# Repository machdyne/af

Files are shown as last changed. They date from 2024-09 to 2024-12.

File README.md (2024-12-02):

# Machdyne AF

## Overview

Machdyne AF is an open-source project for a PNP autofeeder system[^1].

The autofeeder design is a closed-loop system that uses an infrared LED and phototransistor array[^2] to precisely detect the tape position. The tape is moved forward using a geared DC motor and a sprocket. The cover tape is partially separated and advanced with the tape.

The autofeeders can be chained together with 4 wires and communicate with the system controller using the I2C protocol.

The system uses two custom printed circuit board designs. An autofeeder controller PCB (Essen) includes the tape detection and motor driver circuitry for each autofeeder. A system controller PCB (Koch) provides power and allows a chain of feeders to communicate with the OpenPnP software over a USB-C port.

[^1]: This project is still under development and is not yet suitable for use in production.
[^2]: While the PCB has an array of six phototransistors, the firmware is currently using only one.

## Autofeeder 3D parts (AF1)

| Model | Image | Description |
| ----- | ----- | --- |
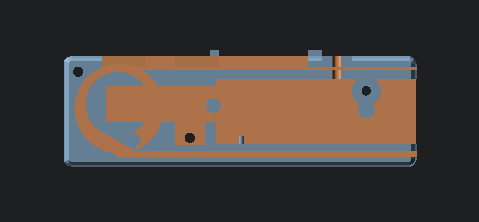
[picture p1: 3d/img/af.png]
| [af](3d/stl/af.stl) |  | The autofeeder body guides the tape and holds the Essen PCB in place |
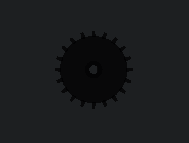
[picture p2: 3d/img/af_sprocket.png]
| [af_sprocket](3d/stl/af_sprocket.stl) |  | The sprocket advances the tape |
| [af_motor_lock](3d/stl/af_motor_lock.stl) | af_motor_lock | The motor lock holds the motor in place |
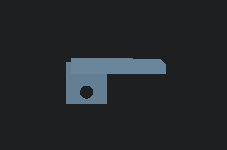
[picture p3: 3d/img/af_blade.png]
af_blade
| [af_blade](3d/stl/af_blade.stl) |  | The blade partially peels the clear film from the top of the tape to the side |
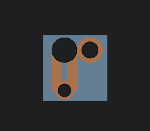
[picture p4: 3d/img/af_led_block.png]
af_led_block
| [af_led_block](3d/stl/af_led_block.stl) |  | The LED block holds the LED in place |
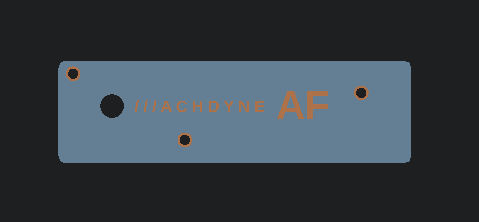
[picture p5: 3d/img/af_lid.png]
af_lid
| [af_lid](3d/stl/af_lid.stl) |  | The lid closes the autofeeder and guides the tape |

### Bill of Materials

| Part | Quantity | Description | Example P/N |
| ---- | --- | --- | --- |
| Worm gear motor | 1 | Right-angle N20 DC 12V 16 RPM | JGY-N20 |
| LED | 1 | 3mm 940nm 1.3Vf Infrared LED | DY-FIR204C |
| M3 bolt 12mm + nut | 1 | for blade | - |
| M3 screw 20mm countersunk | 1 | for LED block | - |
| M3 bolt 20mm countersunk + nut | 3 | for lid | - |
| M3 bolt 25mm | 1 | to connect LED block to rail |
| M3 T3 nut | 1 | to connect LED block to rail |

You will also need dupont jumper wires to connect the motor and LED to Essen.

### Assembly Instructions

Cut, strip and solder one end of the jumper wires to the motor leads and each lead of the LED. Press the LED into the LED block, and run the wires through the large LED block hole.

Attach the blade using an M3 bolt and nut.

Press the sprocket onto the motor axle. Press the motor into the motor cavity.

Run the LED wires through the rear autofeeder hole and connect to Essen LED\_A and LED\_K. Connect the motor wires to Essen MOT1 and MOT2.

Push the PCB onto the PCB notches so that it locks into place.

Attach the LED block using the screw.

Place the motor lock on top of the motor.

Attach the lid.

Connect Essen to Koch or other Essens using a 4-pin female-female 2.54mm dupont cable.

Attach the LED block to a 2020 rail with an M3 bolt and T-nut.

The assembled autofeeder (without lid):

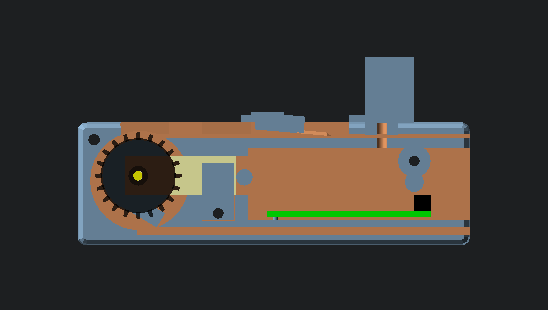
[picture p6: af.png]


## Autofeeder controller PCB (Essen)

Also see the [firmware and usage instructions](fw/essen).

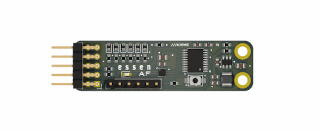
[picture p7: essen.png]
Essen


### Pinout (Rear)

```
9  7  5  3  1
10 8  6  4  2
```

| Pin | Signal | Notes |
| --- | --- | ----- |
| 9/10 | 12V | System power input |
| 7/8 | GND | Ground |
| 5/6 | SDA | I2C data |
| 3/4 | SCL | I2C clock |
| 2 | TRIGGER | Optional external tape advance signal |
| 1 | SWDIO | MCU SWD signal for firmware updates / serial debugging output |

### Pinout (Top)

| Pin | Signal | Notes |
| --- | --- | ----- |
| 1 | MOT1 | Motor driver output #1 |
| 2 | GND | Ground |
| 3 | MOT2 | Motor driver output #2 |
| 4 | GND | Ground |
| 5 | ELED\_A | External (IR) LED anode |
| 6 | ELED\_K | External (IR) LED cathode |

The motor driver can drive one bidirectional motor or two unidirectional motors.

## System controller PCB (Koch)

Also see the [firmware and usage instructions](fw/koch).

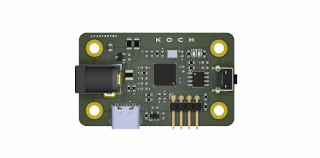
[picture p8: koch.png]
Koch


### Pinout

```
1 2 3 4
```

| Pin | Signal | Notes |
| --- | --- | ----- |
| 1 | 12V | System power output (2.5mm positive tip) |
| 2 | GND | System ground |
| 3 | SDA | I2C data |
| 4 | SCL | I2C clock |

## Funding

This project is being partially funded through the [NGI0 Entrust Fund](https://nlnet.nl/entrust/), a fund established by NLnet with financial support from the European Commission's Next Generation Internet programme.

## License

This project is released under the [CERN-OHL-P](LICENSE.txt) license.

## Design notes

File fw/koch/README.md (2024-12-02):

# Koch Firmware

Koch is the autofeeder system controller PCB for the [Machdyne AF](https://github.com/machdyne/af) project.

This firmwire provides a minimal G-code compatible interface over the USB port that can be driven by an OpenPnP GcodeDriver.

Each feeder has an 1-byte ID, which is set when the Essen firmware is built.

## Building

To build the RP2040 firmware, assuming you have [pico-sdk](https://github.com/raspberrypi/pico-sdk) installed:

```
$ mkdir build
$ cd build
$ cmake ..
$ make
```

## OpenPnp Configuration

### Machine Setup

Add a GCodeDriver under Drivers and set the correct serial port, 115200 baud.

Set the driver Gcode value for ACTUATE\_DOUBLE\_COMMAND:

```
K100 {IntegerValue}
```

Add an Actuator that uses the above driver with Value Type of Double.

### Feeder Setup

Add a new feeder and select the above actuator, set the actuator value to the decimal I2C ID of the feeder.

## Gcode Commands

| Command | Description |
| --- | --- |
| K100 \<feeder\_id\> | Advance the specified feeder (ID is base-10) |
| K200 | Motor on full forward |
| K201 | Motor on full reverse |
| K202 | Motor off |
| K900 | Report system status & current usage |

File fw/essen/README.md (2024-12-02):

# Essen Firmware

Essen is the autofeeder controller PCB for the [Machdyne AF](https://github.com/machdyne/af) project.

This firmware controls the autofeeder and accepts I2C commands from the system controller (Koch).

Each feeder has an 1-byte ID, which is set when the firmware is built.

The sensor may need to be calibrated by changing the AF\_THRES definitions.

## Building

To build the firmware you need to have a RISC-V toolchian installed, see [ch32v003fun](https://github.com/cnlohr/ch32v003fun/wiki/Installation) for setup instructions.

To build the firmware and program Essen (via the SWDIO pin):

```
$ make
```

## License

Essen uses ch32V003fun which is released under the MIT license.

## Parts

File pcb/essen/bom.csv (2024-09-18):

Id | Designator | Footprint | Quantity | Designation | Supplier and ref
1 | R13,R9,R3,R10,R11,R12,R4 | R_0603_1608Metric | 7 | 10K
2 | H1,H2 | MountingHole_2.7mm_M2.5_ISO14580_Pad | 2 | MountingHole_Pad
3 | L1 | L_1210_3225Metric | 1 | 3.3uH 1.2A
4 | U3 | WSON-8-1EP_2x2mm_P0.5mm_EP0.9x1.6mm_ThermalVias | 1 | DRV8220
5 | C9,C10 | C_0603_1608Metric | 2 | 22uF
6 | Q7,Q6,Q4,Q8,Q5,Q3 | D_0603_1608Metric | 6 | Q_Photo_NPN | XL-1608PDC
7 | C8,C6 | C_0603_1608Metric | 2 | 100nF16v
8 | U1 | TSSOP-20_4.4x6.5mm_P0.65mm | 1 | CH32V003F4P6
9 | C3 | C_0805_2012Metric | 1 | 22uF25v
10 | J2 | PinHeader_1x06_P2.54mm_Vertical | 1 | Conn_01x06_Pin
11 | C1 | C_0603_1608Metric | 1 | 100nF
12 | SW3 | Button_2P_3x4mm | 1 | SW_Push
13 | R1 | R_0603_1608Metric | 1 | 1K
14 | F1 | Fuse_0603_1608Metric | 1 | 500mA Hold 1A Trip 15V
15 | C7 | C_0805_2012Metric | 1 | 10uF16v
16 | R6,R7 | R_0603_1608Metric | 2 | 100R
17 | D1 | LED_0603_1608Metric | 1 | LED
18 | U4 | TSOT-23-6 | 1 | AP62300TWU-7
19 | C2 | C_0603_1608Metric | 1 | 10uF
20 | R2 | R_0603_1608Metric | 1 | 33K2
21 | J1 | PinHeader_2x05_P2.54mm_Horizontal | 1 | Conn_02x05_Odd_Even
22 | G*** | ld-kicad | 1 | LOGO

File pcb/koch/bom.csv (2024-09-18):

Id | Designator | Footprint | Quantity | Designation | Supplier and ref
1 | C6,C5,C8,C14,C12,C4,C13,C7 | C_0603_1608Metric | 8 | 100nF
2 | C2,C1 | C_0603_1608Metric | 2 | 15pF
3 | R12,R2,R6 | R_0603_1608Metric | 3 | 5K1
4 | R7 | R_0603_1608Metric | 1 | 10K
5 | C3,C18,C15,C10 | C_0603_1608Metric | 4 | 1uF
6 | J3 | BarrelJack_GCT_DCJ200-10-A_Horizontal | 1 | Barrel_Jack
7 | D2 | LED_0603_1608Metric | 1 | LEDR
8 | R13 | R_1206_3216Metric | 1 | 4K7
9 | R4,R3 | R_0603_1608Metric | 2 | 27R
10 | H1,H4,H2,H3 | MountingHole_3.2mm_M3_ISO14580_Pad | 4 | MountingHole_Pad
11 | R1,R14 | R_0603_1608Metric | 2 | 536R
12 | U2 | SOIC-8_3.9x4.9mm_P1.27mm | 1 | W25Q32JVSS
13 | J2 | PinHeader_1x04_P2.54mm_Horizontal | 1 | Conn_01x04_Pin
14 | F1 | Fuse_1210_3225Metric | 1 | 2.6A HOLD 5A TRIP 24V
15 | U4 | SOT-23 | 1 | ZXCT1107
16 | U3 | TSOP-5_1.65x3.05mm_P0.95mm | 1 | NCP115
17 | D1 | LED_0603_1608Metric | 1 | LEDG
18 | C11 | C_0603_1608Metric | 1 | 10pF50v
19 | C17 | C_0603_1608Metric | 1 | 4.7uF
20 | U1 | RP2040-QFN-56-OFFICIAL | 1 | RP2040
21 | J1 | USB_C_Receptacle_HRO_TYPE-C-31-M-12-BIG-PADS | 1 | TYPE-C-31-M-12-FIXED
22 | R8,R5 | R_0603_1608Metric | 2 | 1K
23 | SW3 | SW_Tactile_SPST_Angled_PTS645Vx39-2LFS | 1 | BOOT
24 | C16 | C_0805_2012Metric | 1 | 22uF16v
25 | R9,R10 | R_0603_1608Metric | 2 | 4K7
26 | R11 | R_1206_3216Metric | 1 | 50mOhm
27 | FB1 | R_0603_1608Metric | 1 | Ferrite_Bead
28 | Y1 | XTAL_ECS-240-8-33-AGN-TR | 1 | ECS-80-12-33-JGN-TR-12MHZ

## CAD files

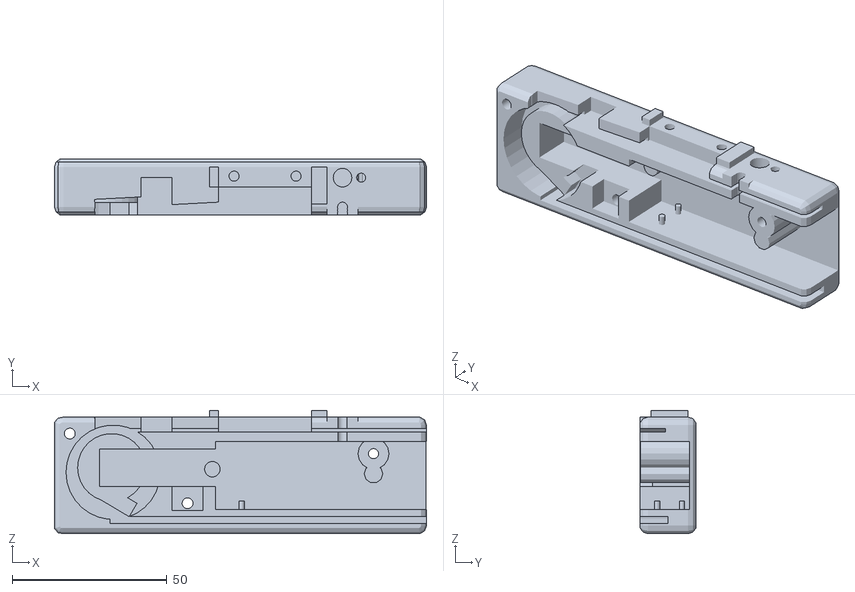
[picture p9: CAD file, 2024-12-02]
3d/stl/af.stl
120.0 x 18.0 x 39.8

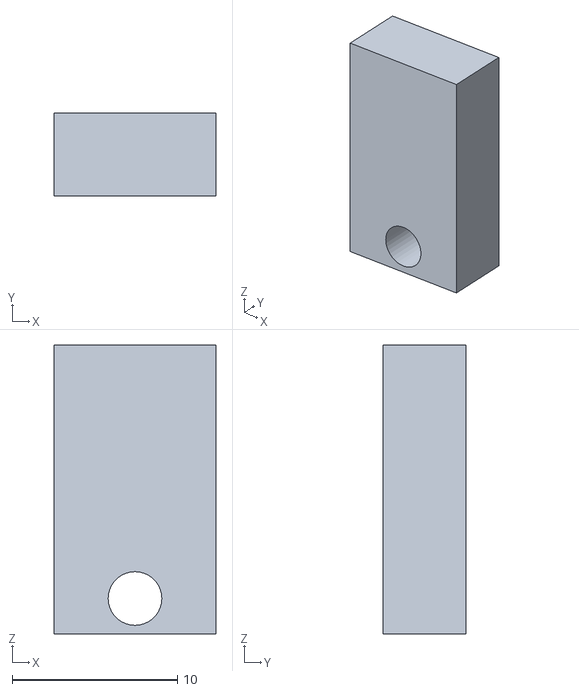
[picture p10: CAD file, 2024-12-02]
3d/stl/af_motor_lock.stl
9.80 x 5.00 x 17.5

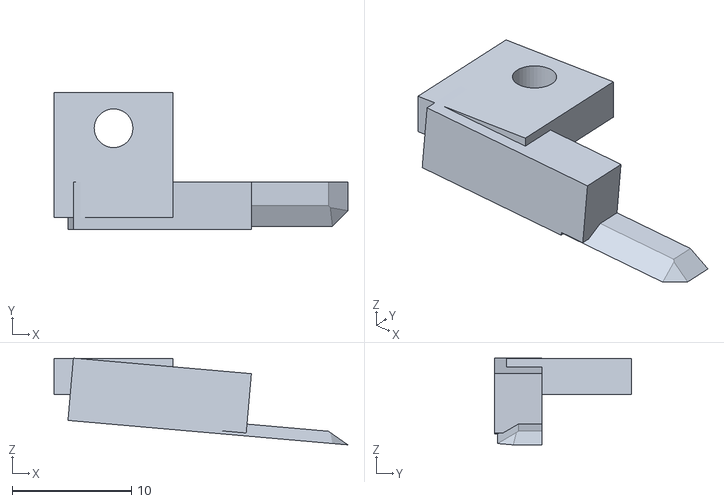
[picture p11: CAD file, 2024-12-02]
3d/stl/af_blade.stl
24.7 x 11.5 x 7.29

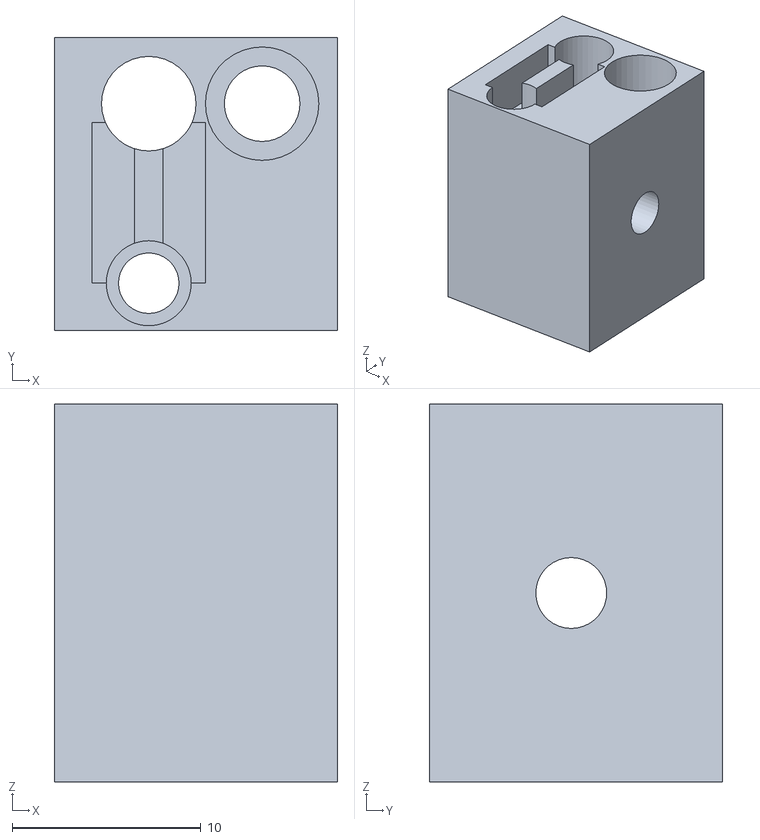
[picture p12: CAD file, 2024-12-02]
3d/stl/af_led_block.stl
15.0 x 15.5 x 20.0

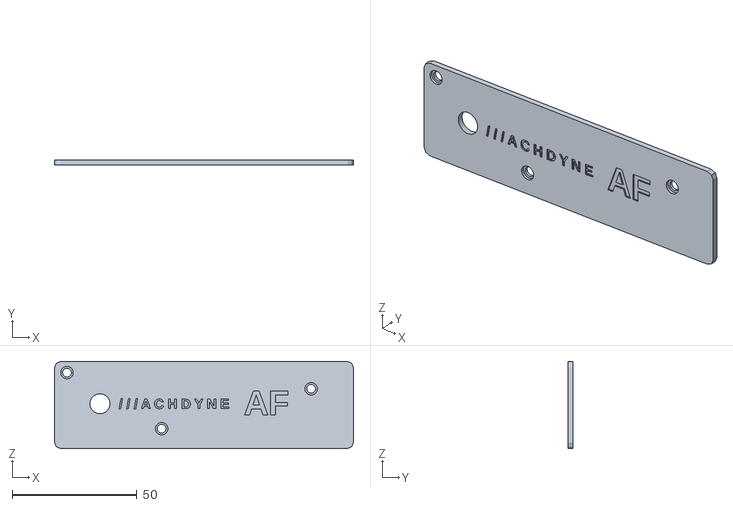
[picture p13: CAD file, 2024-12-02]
3d/stl/af_lid.stl
120.0 x 2.00 x 35.0

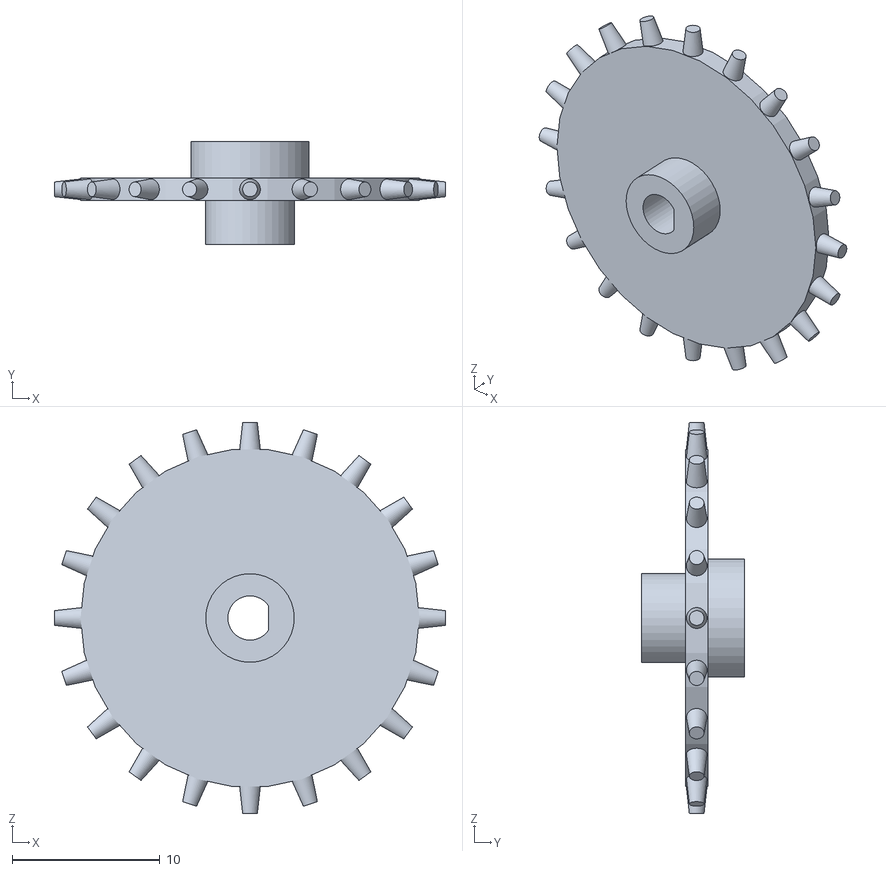
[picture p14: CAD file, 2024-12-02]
3d/stl/af_sprocket.stl
26.5 x 7.00 x 26.5

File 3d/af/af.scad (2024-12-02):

/*
 * PnP Autofeeder
 * Copyright (c) 2024 Lone Dynamics Corporation. All rights reserved.
 * 
 */

tape_width = 8.2;
tape_thickness = 1.2;
tape_pitch = 4;

gear_spokes = 20;
gear_d = gear_spokes * tape_pitch / PI;

rotate([90,0,0]) {
	
	af();

	translate([0,11.75,0]) af_led_block();
	
	af_motor_lock();
	translate([0,0.85,0]) af_blade();
//	translate([0,0.85,0]) af_film_puller();
//	translate([0,0,10]) af_lid();
	
//	translate([-100,12,0.9]) af_tape();

	color([0,0,0,0.5]) rotate([270,0,0]) translate([-44.5,-5,0.5]) af_sprocket();
	
	rotate([270,180,0]) translate([-85,-7,-12]) af_pcb();
	rotate([90,0,180]) translate([22.75,-2,0.5]) af_tape_motor();

}

module af_tape() {
	color([1,1,1]) cube([200,1,8]);
	
}

module af_tape_motor(margin=0) {
	 
	 translate([8.75,0,-0]) color([1,1,0.7]) cube([34, 10+margin, 12+margin], center=true);


	 color([1,1,0]) translate([16.5+9-3.5,8.5,0]) rotate([90,0,0])
		cylinder(d=3, h=7.5, center=true, $fn=36);

}

module af_pcb() {
	color([0,1,0]) translate([40,0,0]) cube([50,15,1.6]);
	color([0,0,0]) translate([40,0,1.6]) cube([5,15,5]);
}

module af_sprocket() {
	gear_spokes = 20;
	difference() {
		union() {
			for (i = [0:gear_spokes-1]) {
				rotate([90,0,90]) translate([-2.75,0,0])
					rotate([i*(360/gear_spokes),0,0])
						translate([0,0,11])
							cylinder(d1=1.5, d2=1, h=2.25, $fn=36);
			}
			rotate([90,0,0]) translate([0,0,2]) cylinder(d=gear_d-2.5, h=1.5);
			rotate([90,0,0]) translate([0,0,-0.5]) cylinder(d=8, h=3.5, $fn=36);
			rotate([90,0,0]) translate([0,0,3]) cylinder(d=6, h=3.5, $fn=36);
			
		}
		rotate([90,0,0]) difference() {
			translate([0,0,2]) cylinder(d=3, h=20, center=true, $fn=36);
			translate([1.75,0,2]) cube([1,10,10], center=true);
		}
		
	}
}

module af_lid() {
	
	difference() {

		union() {
			translate([-126/2,-35/2-1.5,-2/2]) roundedcube(120,35,2,2.5);
		}
		
		// bolt holes
		translate([40,5,-20]) cylinder(d=3.5, h=50, $fn=36);
		translate([-20,-11,-20]) cylinder(d=3.5, h=50, $fn=36);
		translate([-58,11.5,-20]) cylinder(d=3.5, h=50, $fn=36);
		
		// flush mount bolt holes
		translate([40,5,0]) cylinder(d=5, h=50, $fn=36);
		translate([-20,-11,0]) cylinder(d=5, h=50, $fn=36);
		translate([-58,11.5,0]) cylinder(d=5, h=50, $fn=36);

		// axle
		translate([-44.75,0.5,-5]) cylinder(d=8, h=50, $fn=36);

		// logo
		translate([-15,-1.5,0.5])
				linear_extrude(5)
					text("/ / / A C H D Y N E", size=4, halign="center",
						font="Liberation Sans:style=Bold");		

		translate([20,-4,0.5])
				linear_extrude(5)
					text("AF", size=10, halign="center",
						font="Liberation Sans:style=Bold");		
		
	}
}

module af_blade() {
	
	union() {
	
		// blade mount
		difference() {
			translate([-10,16,-6.5]) cube([10,3,10.5]);
			translate([-5,20,-3.5]) rotate([90,0,0])
				cylinder(d=3.25, h=10, $fn=36);
		}
		
		rotate([0,0,-5]) {
			
			translate([-10,13.25,1]) cube([15,5,4]);

			// film blade
			translate([0,0,0]) rotate([0,0,0]) difference() {

				translate([-10,13,1]) cube([25,1,4]);
				translate([11,14.5,0.5]) rotate([0,0,-30]) cube([25,2,4]);
				translate([3,14,3]) rotate([30,0,0]) cube([25,2,4]);
				translate([5,14,10]) rotate([35,45,0]) cube([25,2,4]);

			}

		}
	
	}
}

module af_film_puller() {

			
	union() {
	
		// blade mount
		difference() {
			translate([-10,16,-6.5]) cube([30,19,12]);
			
			// bolt holes
			translate([-5,50,-3.5]) rotate([90,0,0])
				cylinder(d=3.25, h=100, $fn=36);
			translate([15,50,-3.5]) rotate([90,0,0])
				cylinder(d=3.25, h=100, $fn=36);
			
			translate([-5,36,-3.5]) rotate([90,0,0])
				cylinder(d=5, h=2, $fn=36);
			translate([15,36,-3.5]) rotate([90,0,0])
				cylinder(d=5, h=2, $fn=36);
			
			// motor cutout
			translate([5-(12.25/2),28,-5.75]) cube([12.25,50,10.25]);
			translate([5-(10.5/2),29,-5.75]) cube([10.5,50,15.5]);
			
			// gear axle
			translate([5,22,-10]) rotate([0,0,0])
				cylinder(d=3.5, h=50, $fn=36);
				//cylinder(d=3.25, h=50, $fn=36);


	
		}
		
	}


}
		
module af_motor_lock() {
	difference() {
		translate([-25+0.1,-7.25-5.9,3.4]) cube([9.8,17.5,5]);
		translate([-20,-11,-20]) cylinder(d=3.25, h=50, $fn=36);
	}
}

module af_led_block() {
	
	difference() {
		
		// LED block
		translate([25,25,-6.5]) rotate([90,0,0]) cube([15,15.5,20]);

		// LED mount
		translate([30,28,6.5]) rotate([90,0,0]) cylinder(d=4.5, h=15, $fn=36);
		translate([30,28,6.5]) rotate([90,0,0]) cylinder(d=3.2, h=25, $fn=36);
		
		// lead separator
		translate([27,26,-2]) rotate([90,0,0]) cube([2.25,8.5,5]);
		translate([30.75,26,-2]) rotate([90,0,0]) cube([2.25,8.5,5]);
		
		// LED block screw hole
		translate([36,20,-3]) rotate([90,0,0]) cylinder(d=4, h=35, center=true, 
			$fn=36);

		translate([36,24,-3]) rotate([90,0,0]) cylinder(d=6, h=5, center=true, 
			$fn=36);

		// rail mount hole
		translate([36,15,1.5]) rotate([0,90,0]) cylinder(d=3.75, h=35, center=true, $fn=36);

		// wire escape
		translate([30,10,-3]) rotate([90,0,0]) cylinder(d=6, h=35, center=true, 
			$fn=36);
	}

}

module af() {

// rail:
//	color([0,0,0]) translate([50,27,0]) cube([20,20,100], center=true);
	
	difference() {
		translate([40,5,-7.19]) cylinder(d=10, h=16);
		translate([40,5,-20]) cylinder(d=3.25, h=50, $fn=36);
		translate([40,5,-11]) cylinder(d=7, h=5, $fn=6);
	}
	
	translate([40,-9+7.5,-7.19]) cylinder(d=6, h=16);
		
	// blade lock
	translate([-13,19,-6.5]) rotate([90,0,0])
		cube([3,6.5,3]);

	// led block lock
	translate([20,19,-6.5]) rotate([90,0,0])
		cube([5,12,3]);

	// rear motor lock
	translate([-12,0,-8]) cylinder(d=5, h=5, $fn=36);

	difference() {
		translate([-44.5,0.5,0]) cylinder(d=gear_d-3.5, h=5);
		translate([-23.5,0.5,3.25]) {
			cube([50, 12.1, 20.5], center=true);
		}
		

	}
		
	// tape exit guide
	translate([-45.5,-5.55,-0]) rotate([90,0,-30.75]) cube([10.7,5,5]);
	
	// pcb mount notches
	translate([55-57.5,-10.25,-4.5]) rotate([90,0,0])
		cylinder(d=1.75, h=5, $fn=36);
	translate([55-57.5,-13.25,-4.5]) rotate([90,0,0])
		cylinder(d=3, h=1, $fn=36);
	translate([55-57.5,-10.25,-4.5+8]) rotate([90,0,0])
		cylinder(d=1.75, h=5, $fn=36);
	translate([55-57.5,-13.25,-4.5+8]) rotate([90,0,0])
		cylinder(d=3, h=1, $fn=36);

	difference() {
			
		union() {
			
			minkowski() {
				translate([-3,-2,0]) cube([120-5,37.5-5,18-5], center=true);
				sphere(2.6);
			}
			
			// LED block platform
			translate([25,16.81,-6.5]) rotate([90,0,0]) cube([10,15.5,3.75]);
				
		}
		
		// pick position
		translate([-35,12,-3]) cube([10,50,10]);
		
		// film guide
		translate([-50,12,7]) rotate([0,3,0]) cube([50,50,10]);
		translate([-10,12,0]) cube([30,50,20]);
		translate([1,13.1,0]) rotate([0,-30,25]) cube([5,5,5]);

		// film guide post pick
		translate([-50,12,4]) rotate([0,3,0]) cube([20,50,10]);
		
		// blade mount / film motor mount
		translate([-5,20,-3.5]) rotate([90,0,0])
			cylinder(d=3.25, h=15, $fn=36);

		translate([15,20,-3.5]) rotate([90,0,0])
			cylinder(d=3.25, h=15, $fn=36);
		
		// LED light channel
		translate([30,28,6.5]) rotate([90,0,0]) cylinder(d=3.2, h=20, $fn=36);
		translate([30,28,7.5]) rotate([90,0,0]) cylinder(d=3.2, h=20, $fn=36);
		translate([30,28,8.5]) rotate([90,0,0]) cylinder(d=3.2, h=20, $fn=36);
		
		// LED / motor wire escape
		translate([30,10,-3]) rotate([90,0,0]) cylinder(d=6, h=35, center=true, 
			$fn=36);

		// LED block screw hole
		translate([36,20,-3]) rotate([90,0,0]) cylinder(d=2.9, h=25, center=true, 
			$fn=36);

		// bolt holes
		translate([40,5,-20]) cylinder(d=3.5, h=50, $fn=36);
		translate([-20,-11,-20]) cylinder(d=3.5, h=50, $fn=36);
		translate([-58,11.5,-20]) cylinder(d=3.5, h=50, $fn=36);
		
		// nut holes
		translate([40,5,-11]) cylinder(d=7, h=5, $fn=6);
		translate([-20,-11,-11]) cylinder(d=7, h=5, $fn=6);
		translate([-58,11.5,-11]) rotate([0,0,30]) cylinder(d=7, h=5, $fn=6);
					
		// tape entrance cutout
		translate([-45,12,0.8]) cube([200,tape_thickness,tape_width]);
		translate([-45,12,0]) cube([12,tape_thickness,tape_width]);

		// tape exit cutout
		translate([-45,-17.5,0.0]) cube([200,tape_thickness+1,tape_width+1]);

		// motor cutout
		translate([-23.5,0.5,3.25]) {
			cube([50, 12.1, 20.5], center=true);
		}
		
		// motor lock cutout
		translate([-25,-7.25-6,3.4]) cube([10,10,5.6]);

		// sprocket cutout
		translate([-44,-1,0]) cylinder(d=gear_d+5, h=50);
		
		// pcb cutout
		translate([24,-2,1]) cube([70,22,16], center=true);
		
	}
	
}

// https://gist.github.com/tinkerology/ae257c5340a33ee2f149ff3ae97d9826
module roundedcube(xx, yy, height, radius)
{
    translate([0,0,height/2])
    hull()
    {
        translate([radius,radius,0])
        cylinder(height,radius,radius,true);

        translate([xx-radius,radius,0])
        cylinder(height,radius,radius,true);

        translate([xx-radius,yy-radius,0])
        cylinder(height,radius,radius,true);

        translate([radius,yy-radius,0])
        cylinder(height,radius,radius,true);
    }
}

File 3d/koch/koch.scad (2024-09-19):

/*
 * Koch Case
 * Copyright (c) 2024 Lone Dynamics Corporation. All rights reserved.
 *
 * required hardware (stand alone):
 *  - 4 x M3 x 20mm countersunk bolts
 *  - 4 x M3 nuts
 * 
 * required hardware (rail mount):
 *  - 2 x M3 x 20mm countersunk bolts
 *  - 2 x M3 x 25mm countersunk bolts
 *  - 2 x M3 nuts
 *  - 2 x M3 T-nuts
 *
 */

$fn = 100;

board_width = 30;
board_thickness = 1.5;
board_length = 50;
board_height = 1.6;
board_spacing = 2;

wall = 1.5;

top_height = 14;
bottom_height = 6;

translate([wall,wall,0]) afc_board();

translate([0,0,15])
	afc_case_top();

translate([0,0,-15])
	afc_case_bottom();

module afc_board() {
	
	difference() {
		color([0,0.5,0])
			roundedcube(board_width,board_length,board_thickness,5);
		translate([5, 5, -1]) cylinder(d=3.2, h=10);
		translate([5, 45, -1]) cylinder(d=3.2, h=10);
		translate([25, 5, -1]) cylinder(d=3.2, h=10);
		translate([25, 45, -1]) cylinder(d=3.2, h=10);
	}	
	
}

module afc_case_top() {
	

	difference() {
				
		color([0.5,0.5,0.5])
			roundedcube(board_width+(wall*2),board_length+(wall*2),top_height,5);

		// cutouts
			
		translate([1.5,9.5,-2])
			roundedcube(board_width,board_length-16,14.5,5);

		translate([9.5,2,-2])
			roundedcube(board_width-16,board_length,10.25,5);			
	
		translate([wall, wall, 0]) {

			// vents
			translate([25-(15/2),25,0]) rotate([0,0,-10]) cube([10,1,20]);
			translate([25-(15/2),20,0]) rotate([0,0,-10]) cube([10,1,20]);
			translate([25-(15/2),30,0]) rotate([0,0,-10]) cube([10,1,20]);			

			// POWER JACK
			translate([15-(9.5/2),30,-2]) cube([9.5,30,11.25+1.75]);

			// BOOT BUTTON
			translate([15-(7.6/2),-2,-2]) cube([7.6,30,7+1.75]);

			// USBC
			translate([-2,50-15-(10.5/2),-2]) cube([30,10.5,3.5+1.75]);

			// PNP CHAIN CONNECTOR
			translate([-2,50-34.2-(11/2),-2]) cube([30,11,3+1.75]);


			// bolt holes
			translate([5, 5, -21]) cylinder(d=3.5, h=40);
			translate([5, 45, -21]) cylinder(d=3.5, h=40);
			translate([25, 5, -20]) cylinder(d=3.5, h=40);
			translate([25, 45, -21]) cylinder(d=3.5, h=40);

			// flush mount bolt holes
			translate([5, 5, top_height-1.5]) cylinder(d=5.25, h=4);
			translate([5, 45, top_height-1.5]) cylinder(d=5.25, h=4);
			translate([25, 5, top_height-1.5]) cylinder(d=5.25, h=4);
			translate([25, 45, top_height-1.5]) cylinder(d=5.25, h=4);

			// koch text
			rotate(270)
				translate([-25,3.5,top_height-0.5])
					linear_extrude(1)
						text("K O C H", size=4, halign="center",
							font="Ubuntu:style=Bold");

		}
		
	}	
}

module afc_case_bottom() {
	
	difference() {
		color([0.5,0.5,0.5])
			roundedcube(board_width+(wall*2),board_length+(wall*2),bottom_height,5);
		
		// cutouts
		translate([3,10,1.5])
			roundedcube(board_width-3,board_length-17,10,5);
				
		translate([10.5,2.5,1.5])
			roundedcube(board_width-17.5,board_length-2,10,5);

		translate([wall, wall, 0]) {
			
		// board cutout
		translate([0,0,bottom_height-board_height])
			roundedcube(board_width+0.2,board_length+0.2,board_height+1,2.5);

		translate([wall, wall, 0]) {

			// USBC
			translate([30.5,43,5]) cube([10.20,15,10.5+1]);

		}

		// bolt holes
		translate([5, 5, -11]) cylinder(d=3.2, h=25);
		translate([5, 45, -11]) cylinder(d=3.2, h=25);
		translate([25, 5, -11]) cylinder(d=3.2, h=25);
		translate([25, 45, -11]) cylinder(d=3.2, h=25);

		// nut holes
		translate([5, 5, -1]) cylinder(d=7, h=4, $fn=6);
		translate([5, 45, -1]) cylinder(d=7, h=4, $fn=6);
		translate([25, 5, -1]) cylinder(d=7, h=4, $fn=6);
		translate([25, 45, -1]) cylinder(d=7, h=4, $fn=6);

		}
		
	}	
}

// https://gist.github.com/tinkerology/ae257c5340a33ee2f149ff3ae97d9826
module roundedcube(xx, yy, height, radius)
{
    translate([0,0,height/2])
    hull()
    {
        translate([radius,radius,0])
        cylinder(height,radius,radius,true);

        translate([xx-radius,radius,0])
        cylinder(height,radius,radius,true);

        translate([xx-radius,yy-radius,0])
        cylinder(height,radius,radius,true);

        translate([radius,yy-radius,0])
        cylinder(height,radius,radius,true);
    }
}

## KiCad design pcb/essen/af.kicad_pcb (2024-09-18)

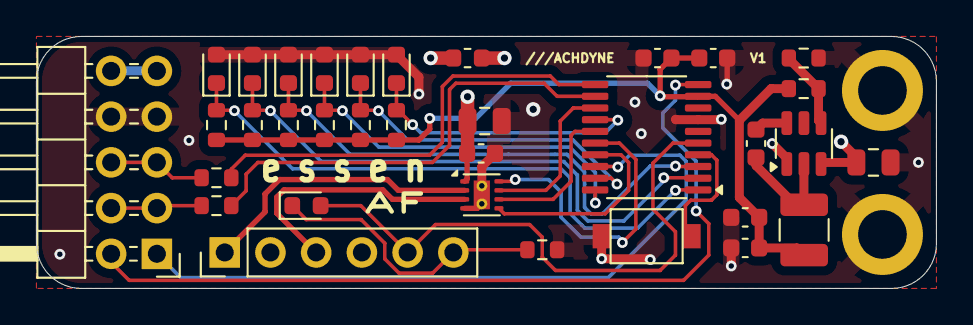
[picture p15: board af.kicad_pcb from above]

Board: 2 copper layers, 50.0 x 14.0 mm, 36 parts (0 on the bottom side), 28 nets.

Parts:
C1: 100nF; C_0603_1608Metric
C2: 10uF; C_0603_1608Metric
C3: 22uF25v; C_0805_2012Metric
C6, C8: 100nF16v; C_0603_1608Metric
C7: 10uF16v; C_0805_2012Metric
C9, C10: 22uF; C_0603_1608Metric
D1: LED; LED_0603_1608Metric
F1: 500mA Hold 1A Trip 15V; Fuse_0603_1608Metric
H1, H2: MountingHole_Pad; MountingHole_2.7mm_M2.5_ISO14580_Pad
J1: Conn_02x05_Odd_Even; PinHeader_2x05_P2.54mm_Horizontal
J2: Conn_01x06_Pin; PinHeader_1x06_P2.54mm_Vertical
L1: 3.3uH 1.2A; L_1210_3225Metric
Q3, Q4, Q5, Q6, Q7, Q8: Q_Photo_NPN; D_0603_1608Metric
R1: 1K; R_0603_1608Metric
R2: 33K2; R_0603_1608Metric
R3, R4, R9, R10, R11, R12, R13: 10K; R_0603_1608Metric
R6, R7: 100R; R_0603_1608Metric
SW3: SW_Push; Button_2P_3x4mm
U1: CH32V003F4P6; TSSOP-20_4.4x6.5mm_P0.65mm
U3: DRV8220; WSON-8-1EP_2x2mm_P0.5mm_EP0.9x1.6mm_ThermalVias
U4: AP62300TWU-7; TSOT-23-6

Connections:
/A2: Q8.1 (C), R13.2, U1.14 (PC4)
/A3: Q7.1 (C), R12.2, U1.19 (PD2)
/A4: Q6.1 (C), R11.2, U1.20 (PD3)
/A5: Q4.1 (C), R9.2, U1.2 (PD5)
/A6: Q5.1 (C), R10.2, U1.3 (PD6)
/A7: Q3.1 (C), R4.2, U1.1 (PD4)
/DRV_IN1: U1.15 (PC5), U3.6 (IN1)
/DRV_IN2: U1.17 (PC7), U3.5 (IN2)
/DRV_MODE: U1.13 (PC3), U3.7 (MODE)
/DRV_SLP: U1.16 (PC6), U3.8 (SLEEP_N)
/ELED_A: D1.2 (A), J2.5, U1.5 (PA1)
/ELED_K: D1.1 (K), J2.6, R1.2
/MOT1: J2.1, U3.2 (OUT1)
/MOT2: J2.3, U3.3 (OUT2)
/PWR3V3: C1.1, C2.1, C9.1, C10.1, L1.2, R2.2, R4.1, R9.1, R10.1, R11.1, R12.1, R13.1, U1.9 (VDD)
/PWRIN: C3.1, C6.1, C7.1, F1.2, U3.1 (VM), U4.3 (VIN)
/PWRINC: F1.1, J1.9, J1.10
/RESET: SW3.1, U1.4 (PD7)
/SCL: R7.2, U1.12 (PC2)
/SCLC: J1.3, J1.4, R7.1
/SDA: R6.2, U1.11 (PC1)
/SDAC: J1.5, J1.6, R6.1
/SW: C8.2, L1.1, U4.2 (SW)
/SWDIO: J1.1, U1.18 (PD1)
/TRIGGER: J1.2, U1.10 (PC0)
GND: C1.2, C2.2, C3.2, C6.2, C7.2, C9.2, C10.2, H1.1, H2.1, J1.7, J1.8, J2.2, J2.4, Q3.2 (E), Q4.2 (E), Q5.2 (E), Q6.2 (E), Q7.2 (E), Q8.2 (E), R1.1, R3.1, SW3.2, U1.7 (VSS), U3.4 (GND), U3.9 (EP), U4.1 (GND)
unnamed: C8.1, U4.6 (BST)
unnamed: R2.1, R3.2, U4.4 (FB)

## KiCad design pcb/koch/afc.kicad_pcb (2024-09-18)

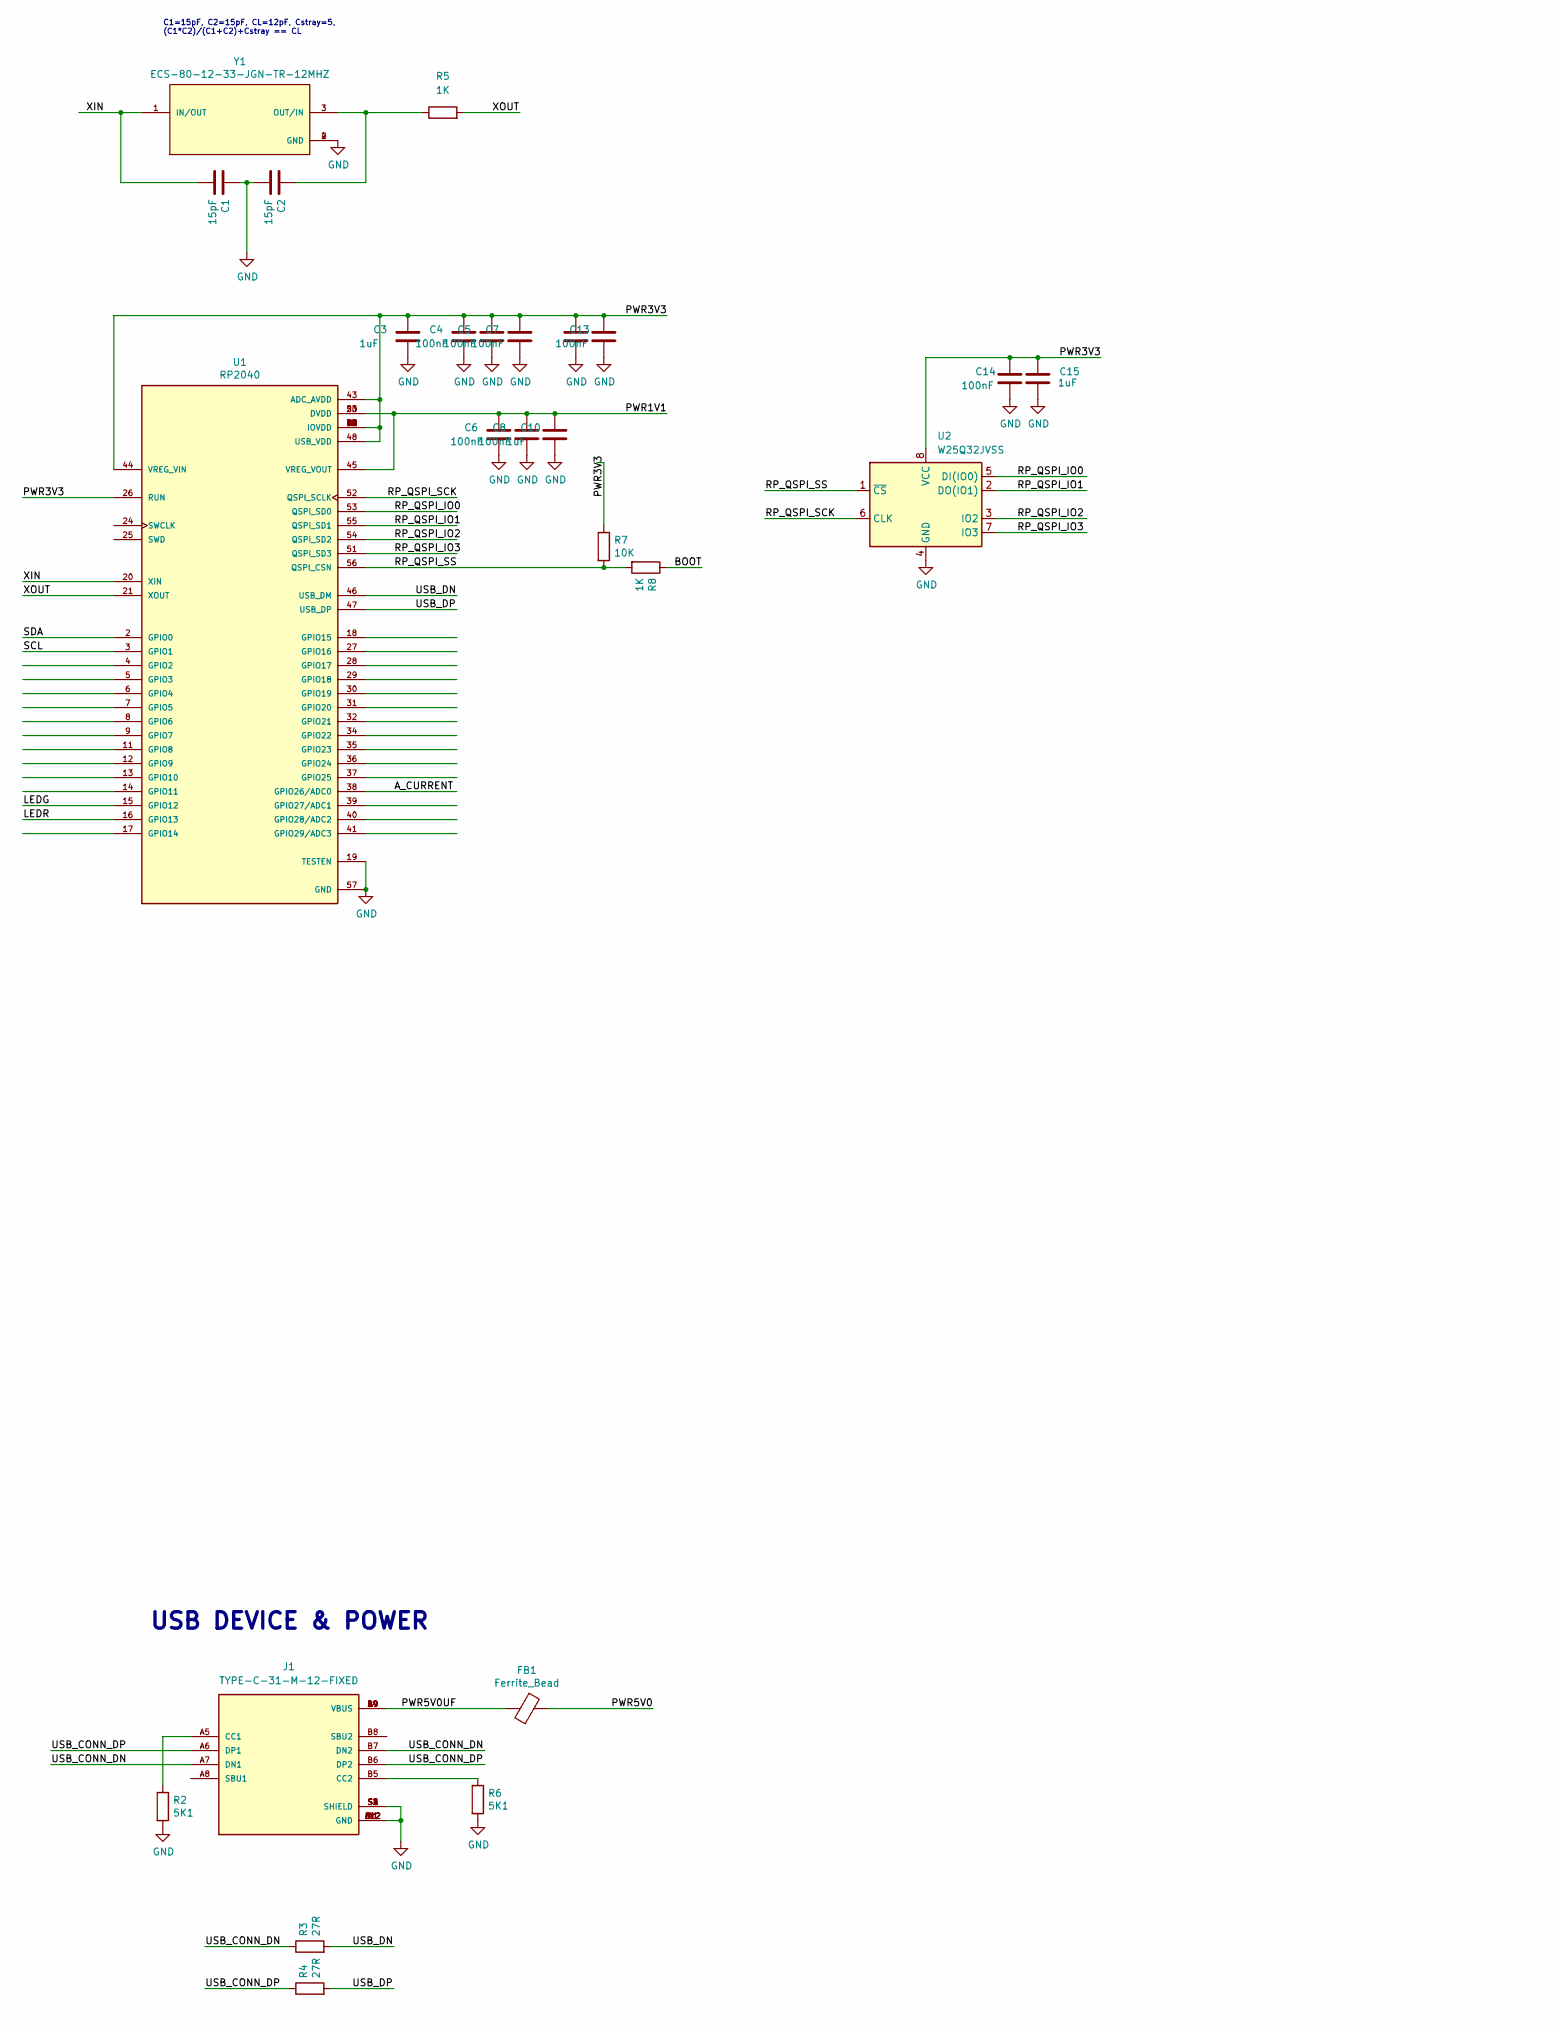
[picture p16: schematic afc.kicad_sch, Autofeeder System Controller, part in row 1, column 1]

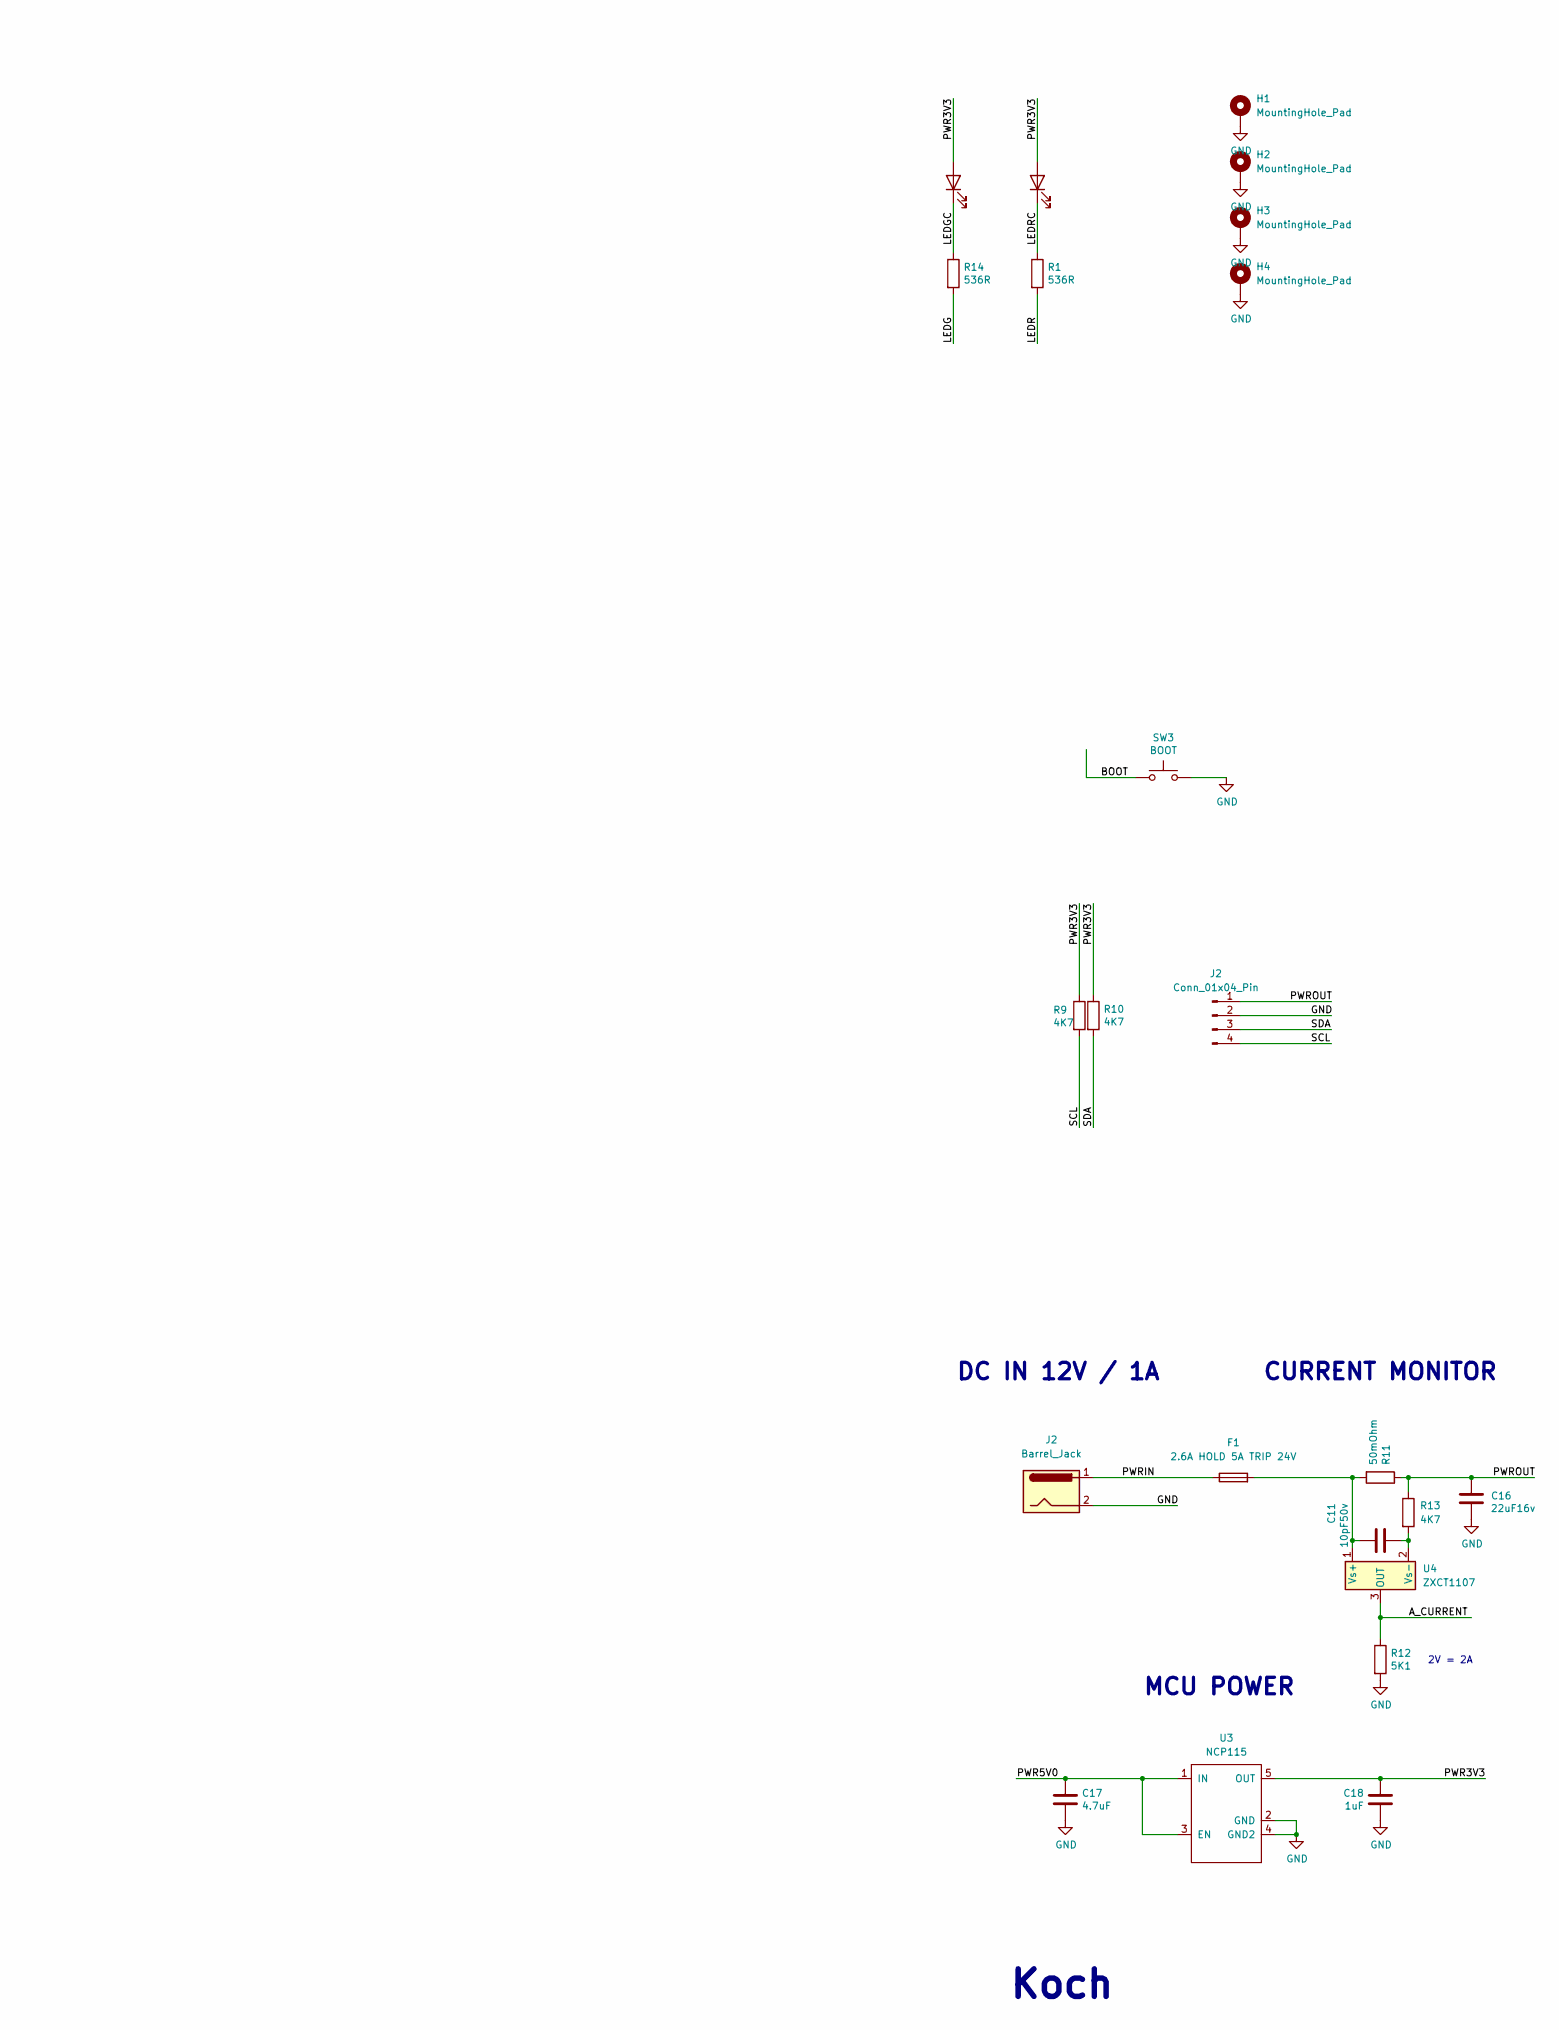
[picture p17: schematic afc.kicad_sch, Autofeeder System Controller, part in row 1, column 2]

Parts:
C1, C2: 15pF; C_0603_1608Metric
C3, C10, C15, C18: 1uF; C_0603_1608Metric
C4, C5, C6, C7, C8, C12, C13, C14: 100nF; C_0603_1608Metric
C11: 10pF50v; C_0603_1608Metric
C16: 22uF16v; C_0805_2012Metric
C17: 4.7uF; C_0603_1608Metric
D1: LEDG; LED_0603_1608Metric
D2: LEDR; LED_0603_1608Metric
F1: 2.6A HOLD 5A TRIP 24V; Fuse_1210_3225Metric
FB1: Ferrite_Bead; R_0603_1608Metric
H1, H2, H3, H4: MountingHole_Pad; MountingHole_3.2mm_M3_ISO14580_Pad
J1: TYPE-C-31-M-12-FIXED; USB_C_Receptacle_HRO_TYPE-C-31-M-12-BIG-PADS; PARTREV A
J2: Barrel_Jack; BarrelJack_GCT_DCJ200-10-A_Horizontal
R1, R14: 536R; R_0603_1608Metric
R2, R6, R12: 5K1; R_0603_1608Metric
R3, R4: 27R; R_0603_1608Metric
R5, R8: 1K; R_0603_1608Metric
R7: 10K; R_0603_1608Metric
R9, R10: 4K7; R_0603_1608Metric
R11: 50mOhm; R_1206_3216Metric
R13: 4K7; R_1206_3216Metric
SW3: BOOT; SW_Tactile_SPST_Angled_PTS645Vx39-2LFS
U1: RP2040; RP2040-QFN-56-OFFICIAL; PARTREV 1.6.1
U2: W25Q32JVSS; SOIC-8_3.9x4.9mm_P1.27mm
U3: NCP115; TSOP-5_1.65x3.05mm_P0.95mm
U4: ZXCT1107; SOT-23
Y1: ECS-80-12-33-JGN-TR-12MHZ; XTAL_ECS-240-8-33-AGN-TR

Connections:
/A_CURRENT: R12.1, U1.38 (GPIO26/ADC0), U4.3 (OUT)
/BOOT: R8.1, SW3.1
/LEDG: R14.2, U1.15 (GPIO12)
/LEDGC: D1.1 (K), R14.1
/LEDR: R1.2, U1.16 (GPIO13)
/LEDRC: D2.1 (K), R1.1
/PWR1V1: C6.1, C8.1, C10.1, U1.23 (DVDD), U1.45 (VREG_VOUT), U1.50 (DVDD)
/PWR3V3: C3.1, C4.1, C5.1, C7.1, C12.1, C13.1, C14.1, C15.1, C18.1, D1.2 (A), D2.2 (A), R7.1, R9.1, R10.1, U1.1 (IOVDD), U1.10 (IOVDD), U1.22 (IOVDD), U1.26 (RUN), U1.33 (IOVDD), U1.42 (IOVDD), U1.43 (ADC_AVDD), U1.44 (VREG_VIN), U1.48 (USB_VDD), U1.49 (IOVDD), U2.8 (VCC), U3.5 (OUT)
/PWR5V0: C17.1, FB1.1, U3.1 (IN), U3.3 (EN)
/PWR5V0UF: FB1.2, J1.A4 (VBUS), J1.A9 (VBUS), J1.B4 (VBUS), J1.B9 (VBUS)
/RP_QSPI_IO0: U1.53 (QSPI_SD0), U2.5 (DI(IO0))
/RP_QSPI_IO1: U1.55 (QSPI_SD1), U2.2 (DO(IO1))
/RP_QSPI_IO2: U1.54 (QSPI_SD2), U2.3 (IO2)
/RP_QSPI_IO3: U1.51 (QSPI_SD3), U2.7 (IO3)
/RP_QSPI_SCK: U1.52 (QSPI_SCLK), U2.6 (CLK)
/RP_QSPI_SS: R7.2, R8.2, U1.56 (QSPI_CSN), U2.1 (~CS)
/SCL: J2.4, R9.2, U1.3 (GPIO1)
/SDA: J2.3, R10.2, U1.2 (GPIO0)
/USB_CONN_DN: J1.A7 (DN1), J1.B7 (DN2), R3.1
/USB_CONN_DP: J1.A6 (DP1), J1.B6 (DP2), R4.1
/USB_DN: R3.2, U1.46 (USB_DM)
/USB_DP: R4.2, U1.47 (USB_DP)
/XIN: C1.2, U1.20 (XIN), Y1.1 (IN/OUT)
/XOUT: R5.2, U1.21 (XOUT)
GND: C1.1, C2.2, C3.2, C4.2, C5.2, C6.2, C7.2, C8.2, C10.2, C12.2, C13.2, C14.2, C15.2, C16.2, C17.2, C18.2, H1.1, H2.1, H3.1, H4.1, J1.A1 (GND), J1.A12 (GND), J1.B1 (GND), J1.B12 (GND), J1.S1 (SHIELD), J1.S2 (SHIELD), J1.S3 (SHIELD), J1.S4 (SHIELD), J2.2, R2.2, R6.2, R12.2, SW3.2, U1.19 (TESTEN), U1.57 (GND), U2.4 (GND), U3.2 (GND), U3.4 (GND2), Y1.2 (GND), Y1.4 (GND); also elsewhere on the board
unnamed: J1.A5 (CC1), R2.1
unnamed: J1.B5 (CC2), R6.1
unnamed: C11.1, F1.2, R11.2, U4.1 (Vs+)
unnamed: C11.2, R13.2, U4.2 (Vs-)
unnamed: C2.1, R5.1, Y1.3 (OUT/IN)

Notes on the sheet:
MCU POWER
C1=15pF, C2=15pF, CL=12pF, Cstray=5, (C1*C2)/(C1+C2)+Cstray == CL
Koch
USB DEVICE & POWER
2V = 2A
CURRENT MONITOR
DC IN 12V / 1A

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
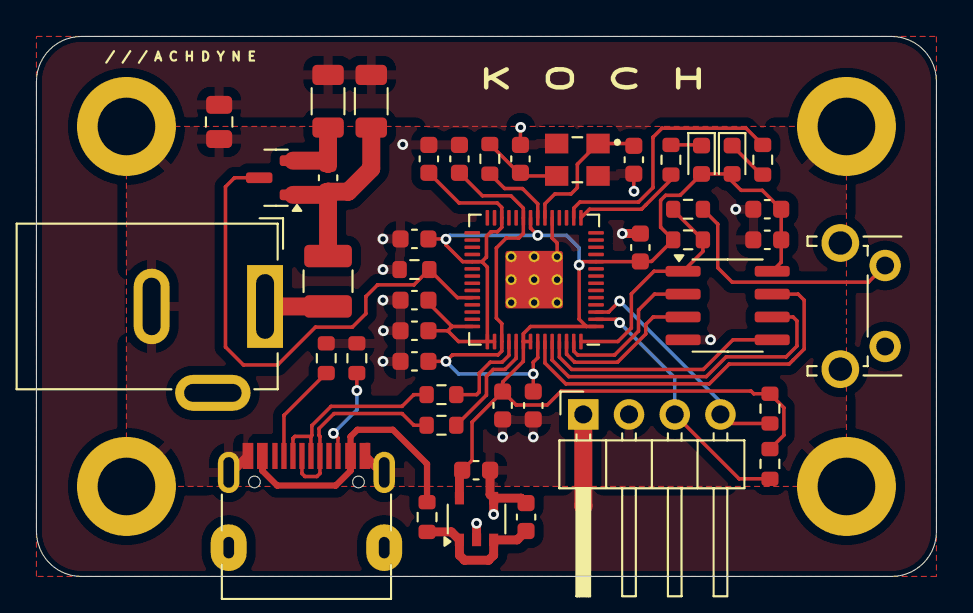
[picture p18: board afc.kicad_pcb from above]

Board: 2 copper layers, 50.0 x 30.0 mm, 48 parts (0 on the bottom side), 32 nets.

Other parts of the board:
J3: Barrel_Jack; BarrelJack_GCT_DCJ200-10-A_Horizontal

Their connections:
GND: J3.2; also elsewhere on the board

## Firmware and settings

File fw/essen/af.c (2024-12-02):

/*
 * Essen Autofeeder Firmware
 * Copyright (c) 2024 Lone Dynamics Corporation. All rights reserved.
 *
 */

#include "ch32v003fun.h"
#include "i2c_slave.h"
#include <stdio.h>

#define AF_I2C_ADDR	0x9

#define AF_ELED_PORT GPIOA
#define AF_ELED_PIN 1

#define AF_DRVMODE_PORT GPIOC
#define AF_DRVMODE_PIN 3

#define AF_DRV1_PORT GPIOC
#define AF_DRV1_PIN 5

#define AF_DRV2_PORT GPIOC
#define AF_DRV2_PIN 7

#define AF_DRVSLPN_PORT GPIOC
#define AF_DRVSLPN_PIN 6

#define AF_I2C_SDA_PORT GPIOC
#define AF_I2C_SDA_PIN 1

#define AF_I2C_SCL_PORT GPIOC
#define AF_I2C_SCL_PIN 2

volatile uint8_t i2c_regs[32] = {0x00};

void i2c_onWrite(uint8_t reg, uint8_t length);
void i2c_onRead(uint8_t reg);

void adc_init( void )
{
	// ADCCLK = 24 MHz => RCC_ADCPRE = 0: divide by 2
	RCC->CFGR0 &= ~(0x1F<<11);

	// Enable ADC
	RCC->APB2PCENR |= RCC_APB2Periph_ADC1;
	
	// PD4 is analog input chl 7
	GPIOD->CFGLR &= ~(0xf<<(4*4));	// CNF = 00: Analog, MODE = 00: Input
	
	// Reset the ADC to init all regs
	RCC->APB2PRSTR |= RCC_APB2Periph_ADC1;
	RCC->APB2PRSTR &= ~RCC_APB2Periph_ADC1;
	
	// Set up single conversion for chl 7
	ADC1->RSQR1 = 0;
	ADC1->RSQR2 = 0;
	//ADC1->RSQR3 = 7;	// 0-9 for 8 ext inputs and two internals
	ADC1->RSQR3 = 6;	// 0-9 for 8 ext inputs and two internals
	
	// set sampling time for chl 7
	ADC1->SAMPTR2 &= ~(ADC_SMP0<<(3*7));
   // Possible times: 0->3,1->9,2->15,3->30,4->43,5->57,6->73,7->241 cycles
   ADC1->SAMPTR2 = 1/*9 cycles*/ << (3/*offset per channel*/ * 7/*channel*/);

	// turn on ADC and set rule group to sw trig
	ADC1->CTLR2 |= ADC_ADON | ADC_EXTSEL;

	// Reset calibration
	ADC1->CTLR2 |= ADC_RSTCAL;
	while(ADC1->CTLR2 & ADC_RSTCAL);
	
	// Calibrate
	ADC1->CTLR2 |= ADC_CAL;
	while(ADC1->CTLR2 & ADC_CAL);
	
	// should be ready for SW conversion now
}

uint16_t adc_get( void )
{
	// start sw conversion (auto clears)
	ADC1->CTLR2 |= ADC_SWSTART;
	
	// wait for conversion complete
	while(!(ADC1->STATR & ADC_EOC));
	
	// get result
	return ADC1->RDATAR;
}

int main()
{
	uint8_t dir;
	uint32_t count = 0;

	SystemInit();
	funGpioInitAll();

	printf("\r\r\n\nessen firmware\n\r");

	// motor driver #1
	(AF_DRV1_PORT)->CFGLR &= ~(0xf<<(4*AF_DRV1_PIN));
	(AF_DRV1_PORT)->CFGLR |= (GPIO_Speed_10MHz | GPIO_CNF_OUT_PP)<<(4*AF_DRV1_PIN);

	// motor driver #2
	(AF_DRV2_PORT)->CFGLR &= ~(0xf<<(4*AF_DRV2_PIN));
	(AF_DRV2_PORT)->CFGLR |= (GPIO_Speed_10MHz | GPIO_CNF_OUT_PP)<<(4*AF_DRV2_PIN);

	// motor mode (floating = h-bridge)
	//(AF_DRVMODE_PORT)->CFGLR &= ~(0xf<<(4*AF_DRVMODE_PIN));
	//(AF_DRVMODE_PORT)->CFGLR |= (GPIO_CNF_IN_FLOATING)<<(4*AF_DRVMODE_PIN);

	// motor mode (low = full-bridge pwm)
	(AF_DRVMODE_PORT)->CFGLR &= ~(0xf<<(4*AF_DRVMODE_PIN));
	(AF_DRVMODE_PORT)->CFGLR |= (GPIO_CNF_IN_FLOATING)<<(4*AF_DRVMODE_PIN);
	(AF_DRVMODE_PORT)->BSHR = (1 << (16+AF_DRVMODE_PIN));

	// driver sleep disable
	(AF_DRVSLPN_PORT)->CFGLR &= ~(0xf<<(4*AF_DRVSLPN_PIN));
	(AF_DRVSLPN_PORT)->CFGLR |= (GPIO_Speed_10MHz | GPIO_CNF_OUT_PP)<<(4*AF_DRVSLPN_PIN);
	(AF_DRVSLPN_PORT)->BSHR = (1 << AF_DRVSLPN_PIN);


	// configure IR LED
	(AF_ELED_PORT)->CFGLR &= ~(0xf<<(4*AF_ELED_PIN));
	(AF_ELED_PORT)->CFGLR |= (GPIO_Speed_10MHz | GPIO_CNF_OUT_PP)<<(4*AF_ELED_PIN);

	// configure I2C slave
   funPinMode(PC1, GPIO_CFGLR_OUT_10Mhz_AF_OD); // SDA
   funPinMode(PC2, GPIO_CFGLR_OUT_10Mhz_AF_OD); // SCL

	SetupI2CSlave(AF_I2C_ADDR, i2c_regs, sizeof(i2c_regs),
		i2c_onWrite, i2c_onRead, false);

//	printf("waiting 1 second ...\n\r");
//	Delay_Ms( 1000 );

	// init adc
	adc_init();

	while(1)
	{
		printf("WAITING FOR COMMAND\n\r");
		Delay_Ms( 2000 );
	}

}

void moveTapeMotor(int ms) {
	(AF_DRV1_PORT)->BSHR = (1 << AF_DRV1_PIN);
   Delay_Ms(ms);
   (AF_DRV1_PORT)->BSHR = ( 1 << (16 + AF_DRV1_PIN) );
}

#define AF_THRES_START 1010
#define AF_THRES_HOLE_MIN 985
#define AF_THRES_HOLE_MAX 995

void moveTapeToPickPosition() {

	// LED on
	(AF_ELED_PORT)->BSHR = (1 << AF_ELED_PIN);
	Delay_Ms(10);

	int start = 1;
	int breakOnMark = 0;
	int tapeEnd = 0;

	while (1) {

		int av = adc_get();

		printf(" ADC: %d\r\n", av);

		if (av > AF_THRES_START) { start = 0; }

		if (!start && av >= AF_THRES_HOLE_MIN && av <= AF_THRES_HOLE_MAX) {
			printf("MARK FOUND\r\n");
			break;
		}

		moveTapeMotor(5);
		Delay_Ms(10);

	}

	// LED off
	(AF_ELED_PORT)->BSHR = ( 1 << (16 + AF_ELED_PIN) );
	Delay_Ms(10);

}

void i2c_onWrite(uint8_t reg, uint8_t length) {
	printf("i2c_onWrite reg: %x len: %x val: %x\n\r", reg, length,
		i2c_regs[reg]);
	if (reg == 0x10) {
		moveTapeToPickPosition();
	} else if (reg == 0x20) {	// forward
		(AF_DRV1_PORT)->BSHR = (1 << AF_DRV1_PIN);
   	(AF_DRV2_PORT)->BSHR = (1 << (16 + AF_DRV2_PIN));
	} else if (reg == 0x21)	{	// reverse
   	(AF_DRV1_PORT)->BSHR = (1 << (16 + AF_DRV1_PIN));
		(AF_DRV2_PORT)->BSHR = (1 << AF_DRV2_PIN);
	} else if (reg == 0x22) {	// off
   	(AF_DRV1_PORT)->BSHR = (1 << (16 + AF_DRV1_PIN));
   	(AF_DRV2_PORT)->BSHR = (1 << (16 + AF_DRV2_PIN));
	}
}

void i2c_onRead(uint8_t reg) {
	printf("i2c_onRead reg: %x val: %x\n\r", reg, i2c_regs[reg]);
}

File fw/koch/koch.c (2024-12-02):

/*
 * Koch Firmware
 * Copyright (c) 2024 Lone Dynamics Corporation. All rights reserved.
 *
 */

#include <stdio.h>
#include <stdlib.h>
#include <stdbool.h>
#include <string.h>
#include <strings.h>
#include <ctype.h>

#include "pico/stdlib.h"
#include "hardware/watchdog.h"
#include "hardware/adc.h"
#include "hardware/i2c.h"
#include "pico/stdlib.h"
#include "pico/binary_info.h"

// Koch GPIOs
#define KOCH_SDA		0
#define KOCH_SCL		1
#define KOCH_LEDG		12
#define KOCH_LEDR		13
#define KOCH_CSENSE	26

// I2C registers for Essen
#define ESSEN_REG_STATUS		0x00	// RO
#define ESEEN_REG_FAULT			0x01	// RO
#define ESSEN_REG_ADVANCE		0x10	// RW
#define ESSEN_REG_MOTOR_FWD	0x20	// RW
#define ESSEN_REG_MOTOR_REV	0x21	// RW
#define ESSEN_REG_MOTOR_OFF	0x22	// RW

#define BUFLEN 32

float koch_adc_current(void);
void koch_i2c_scan(void);
void koch_i2c_set(uint8_t addr, uint8_t reg, uint8_t val);
void koch_i2c_get(uint8_t addr, uint8_t reg, uint8_t *out, uint16_t len);
void koch_report(void);
void koch_parse(char *buf);

int main(void) {

	stdio_init_all();
	while (!stdio_usb_connected()) {
		sleep_ms(100);
	}

	printf("# koch initializing ...\r\n");

	// configure I2C pins
	i2c_init(i2c_default, 100 * 1000);
	gpio_set_function(KOCH_SDA, GPIO_FUNC_I2C);
	gpio_set_function(KOCH_SCL, GPIO_FUNC_I2C);
	// koch has external I2C pull-ups
	gpio_set_pulls(KOCH_SDA, false, false);
	gpio_set_pulls(KOCH_SCL, false, false);

	// configure ADC pins
	adc_init();
	adc_gpio_init(KOCH_CSENSE);
	gpio_set_pulls(KOCH_CSENSE, false, false);

	// parser
   char buf[BUFLEN];
   int bptr = 0;
   int c;

	bzero(buf, BUFLEN);

	// wait for commands
	while (1) {

		c = getchar();

		if (c > 0) {

			if (c == 0x0a || c == 0x0d) {
				putchar(0x0a);
				putchar(0x0d);
				fflush(stdout);
				koch_parse(buf);
				bptr = 0;
				bzero(buf, BUFLEN);
				continue;
			}

			if (bptr >= BUFLEN - 1) {
				printf("# buffer overflow\r\n");
				bptr = 0;
				bzero(buf, BUFLEN);
				continue;
			}

			putchar(c);
			fflush(stdout);
			buf[bptr++] = c;

		}

	}

	return 0;

}


void koch_parse(char *buf) {

	if (!strncmp(buf, "K100", 4)) {
		int id = strtol(buf+5, NULL, 10);
		printf("# advancing tape on feeder id %i ...\r\n", id);
		koch_i2c_set(id, ESSEN_REG_ADVANCE, 0x01);
	} else if (!strncmp(buf, "K200", 4)) {
		int id = strtol(buf+5, NULL, 10);
		printf("# motor (#1 / forward) on feeder id %i ...\r\n", id);
		koch_i2c_set(id, ESSEN_REG_MOTOR_FWD, 0x01);
	} else if (!strncmp(buf, "K201", 4)) {
		int id = strtol(buf+5, NULL, 10);
		printf("# motor (#2 / reverse) on feeder id %i ...\r\n", id);
		koch_i2c_set(id, ESSEN_REG_MOTOR_REV, 0x01);
	} else if (!strncmp(buf, "K202", 4)) {
		int id = strtol(buf+5, NULL, 10);
		printf("# motor(s) lock / off feeder id %i ...\r\n", id);
		koch_i2c_set(id, ESSEN_REG_MOTOR_OFF, 0x01);
	} else if (!strncmp(buf, "K900", 4)) {
		printf("# status report\r\n");
		koch_report();
	} else {
		printf("# unknown command\r\n");
	}

}

void koch_report(void) {

	// 2V = 2A
	float current = koch_adc_current();
	printf("CURRENT: %f amps\n", current);

	koch_i2c_scan();

}

float koch_adc_current(void) {
	const float conversion_factor = 3.3f / (1 << 12);
	adc_select_input(0);
	return(adc_read() * conversion_factor);
}

void koch_i2c_scan(void) {

	printf("\nI2C Bus Scan\n");
	printf("   0  1  2  3  4  5  6  7  8  9  A  B  C  D  E  F\n");

	for (int addr = 0; addr < (1 << 7); ++addr) {
		if (addr % 16 == 0) {
			printf("%02x ", addr);
		}

		// Perform a 1-byte dummy read from the probe address. If a slave
		// acknowledges this address, the function returns the number of bytes
		// transferred. If the address byte is ignored, the function returns
		// -1.

		// Skip over any reserved addresses.
		int ret;
		uint8_t rxdata;

		ret = i2c_read_timeout_us(i2c_default, addr, &rxdata, 1, false,
				1000);

		printf(ret < 0 ? "." : "@");
		printf(addr % 16 == 15 ? "\n" : "  ");

	}

}

void koch_i2c_set(uint8_t addr, uint8_t reg, uint8_t val) {

	int ret;
	uint8_t buf[2];

	buf[0] = reg;
	buf[1] = val;

	ret = i2c_write_blocking(i2c_default, addr, buf, 2, false);

}

void koch_i2c_get(uint8_t addr, uint8_t reg, uint8_t *out, uint16_t len) {

	int ret;
	uint8_t buf[1];

	buf[0] = reg;

	ret = i2c_write_blocking(i2c_default, addr, buf, 1, true);
	ret = i2c_read_blocking(i2c_default, addr, out, len, false);

}

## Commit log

2024-09-19 update hardware notes
    [koch.scad]
2024-12-02 add 3d parts
    [af.scad, af_blade.stl, af_led_block.stl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]
2024-12-02 add missing part
    [af.stl]

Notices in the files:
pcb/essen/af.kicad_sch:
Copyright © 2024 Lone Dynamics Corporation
